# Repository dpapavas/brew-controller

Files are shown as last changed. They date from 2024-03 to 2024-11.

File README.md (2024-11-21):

<!-- -*- coding: utf-8 -*- -->

# Brew controller

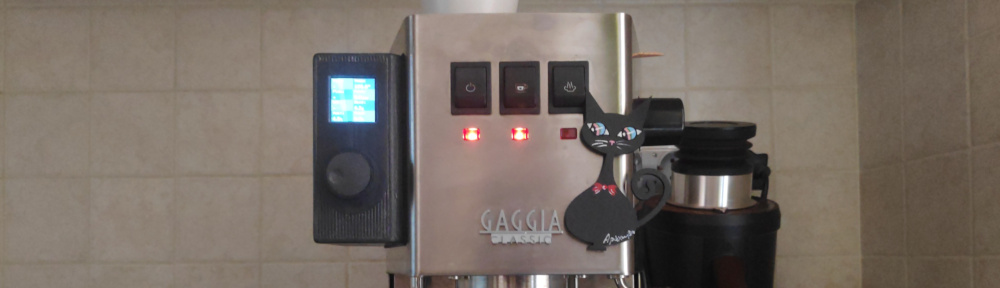
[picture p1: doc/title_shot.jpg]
Title shot


This is a controller module designed as an add-on to the Gaggia Classic espresso
machine, although from a functional perspective it can be used with any "dumb"
espresso machine, i.e. any machine with a simple thermostat for boiler
temperature control and a simple on/off switch for pump control.  It can control
the brew process in both an automatic mode, following a programmed brew profile
based on flow, pressure and/or yield weight, or in manual mode, allowing direct,
real-time control of flow, pressure, or pump power.

## Design

The controller consists of the following parts:

* A pressure sensor, attached to the exit of the boiler, just before the group
  head.

* A flow sensor, attached to the pump inlet.

* A load cell, mounted below the drip tray, weighing the yielded coffee.

* A controller board, consisting of a pair of TRIAC switches, controlling power
  to the boiler and pump and a microcontroller, interfacing the sensors and
  controlling these switches.

* An enclosure and other assorted accessories, used to mount all the above to
  the espresso machine.

The design is freely available, but anyone considering their own build is urged
to read the discussion below, as there are some issues that will need to be
addressed.

## Operation

So, is this useful?  Well, yes, it is. All features, while arguably not
necessary, do offer additional useful control over the brewing process.
Temperature control improves temperature stability and control, allowing the
brewing to be adapted to the coffee at hand and, more importantly, improving the
consistency of the result across multiple shots.  Pump power control, makes
preinfusion possible and, in combination with pressure and flow measurement, it
also makes control of these parameters possible.  Pressure control is useful to
avoid channeling, while flow control can be useful, both to control preinfusion
where pressure has not yet developed and to give some control over brew time.
Weighing the yield allows automatic control of the brew ratio, as well as more
sensible variation of other parameters during the brew process (for instance the
pressure can be tapered off during the final third of the shot in terms of the
yield mass, instead of time).

The following plot is from data recorded by the controller during a programmed
shot.

Shot graph

The machine is already warmed up, as can be seen by the stable temperature (1)
and the small (less than 5% of the total) power needed at the boiler to maintain
it (2).  At about 12s the brew switch is pressed and the shot starts with a
preinfusion phase (3).  The pump is engaged at low power to push water through
the grounds at 3 ml/s.  As this happens, the temperature starts to drop, as cold
water enters the boiler, and power to the boiler is increased in order to
compensate.  Pressure gradually develops as the grounds expand and at 4 bars the
preinfusion phase is terminated (4).  Power to the pump is cut off, flow
vanishes and yield mass starts to rise as coffee starts to drip into the cup.

A blooming phase follows for the next 30s (5), where nothing much happens, apart
from temperature stabilization, a gradual drop-off in pressure and slight
increase in yield, as coffee leaks into the cup.  At 54s, the pump is engaged
once more, at higher power, and pressure is gradually ramped up to 9 bars (6).
Note the high initial flow, as the brew chamber is refilled, followed by a sharp
fall-off as the puck is compressed and pressure develops leading to oscillations
as the PID struggles somewhat to adapt to the complex dynamics.  This
necessitates both a gradual ramp-up in pressure (here from 0 to 9 bars in 5s) as
well as an additional wait time of 5s at 9 bars, while the flow settles.  After
that (7) the brew proceeds at constant flow rate, keeping the flow steady at the
1.7 ml/s it settled at.

In this particular shot, this strategy fails partially.  Maintaining the flow at
the instantaneous value measured at the end of the settling wait interval, leads
to a higher than desired flow and a pressure increase to a bit above 10 bars.
This can be corrected manually, if desired, either by reducing the flow to reduce
the developed pressure, or by reducing the pressure immediately.  No such action
has been taken here and the shot proceeds at a constant 10 bars and about 1.7
ml/s.  Note the disparity in volume and mass, the former of which is calculated
from the flow sensor, while the latter is measured via the load cell.  Some of
the difference is due to the water retained by the grounds, although most of
that has been accounted for, when the volume was reset at the end of the
preinfusion phase (4).  The rest of the difference is owed to inaccuracies in
the flow sensor, which accumulate as its signal is integrated to get the volume.

Finally the brew process is stopped at about 89s, with a total yield of 50g (8)
and pressure and flow drop to zero.  The sudden uptick in mass, is due to the
water remaining in the chamber being evacuated to the drip tray, via the
three-way solenoid valve.

A video recording of the controller brewing this exact shot, can be found
[here](https://youtu.be/QHlgAWKq7i8).

## Build

Although the design works quite well and is, at the time of this writing,
seemingly bug-free and refined enough for efficient and hassle-free daily use,
it does unfortunately suffer from a few design flaws that make it unsuitable for
anyone who might be considering building it.

For one, it was designed by someone that is not an electrical engineer.
Although as much care as possible was taken to ensure a good design, including
simulations and proper calculations where appropriate, the result does have a
few shortcomings which will probably need to be addressed:

* It is based on a Teensy 3.1/3.2 microcontroller, which is sadly no longer in
  production.  Any builds will therefore need to be ported to a more modern
  controller.  This problem is further compounded by the fact that the source
  code is "bare-metal", i.e. no hardware abstraction libraries are used, so that
  porting to a different controller is a non-trivial task.  Note though, that
  teasing out the application specific-code, i.e. the code implementing PID
  control, sensor signal reading and conditioning and rewriting the
  machine-specific parts, such as SPI, I2C, GPIO, timing and interrupt handling
  using a high-level library for the target controller, should not be a
  particularly hard task, given some experience.

* The coffee machine's brew switch, i.e. the one turning on the pump and
  starting the brewing process, is read through a GPIO input that is grounded
  via the switch.  The current design depends on the internal pull-up for this,
  which is too weak and hence prone to EMI.  This should probably be addressed in
  a potential board redesign, by including a stronger external pull-up resistor.

* In the current design, brewing is still controlled by the machine's brew
  switch, which is responsible for turning power to the pump on and off.  While
  this power can then be further controlled via the TRIAC, the three-way
  solenoid valve that is controlled by the same switch cannot.  Relegating this
  task to a relay, controlled by an additional GPIO output could therfore be
  useful, as it would allow automatically stopping the brew process, for
  instance when the desired yield has been achieved.  While this can be done
  now, one still needs to turn the switch off, to turn off the solenoid.  Doing
  this after the pump has been cut off, results in low pressure in the brew
  chamber and hence incomplete evacuation of the remaining brew water,
  nullifying the solenoid valve.

Due to the above, it is not expected that this design will be built by others.
The following discussion will therefore be limited to a general outline of the
build process.  Anyone intending to attempt a build is welcome to open an issue
for further clarifications.

### Parts

The parts needed to populate the board are the following:

|Designator|Description|
|---|---|
|R3,R4|22KΩ, 1W through-hole resistor|
|R5|10KΩ, 1/4W through-hole resistor|
|U5|LD1117, 3.3V, TO-220-3 voltage regulator|
|C4,C2,C5|100nF through-hole ceramic resistor|
|D1|DB104, 400V, 1A bridge rectifier|
|R7,R6|360Ω, 1W through-hole resistor|
|Q1,Q2|2N7000, 0.2A, TO-92 N-Channel MOSFET|
|R8|680Ω, 1W through-hole resistor|
|U3,U2|MOC3021M, 400V optocoupler|
|Q3,Q4|BTA16-800CW 800V, TO-220-3 TRIAC|
|U4|Adafruit MAX31865 Module, or compatible|
|J4|JST XH 2-pin vertical connector|
|R2,R1|82Ω, 1/4W through-hole resistor|
|J2|Pin header, 2.54mm|
|J3|Pin header, 2.54mm|
|J5|Pin header, 2.54mm|
|U1|EL817 or PC817 optocoupler|
|C3|10u radial through-hole capacitor (low profile)|
|U6|Teensy 3.1 or 3.2|
|C1|100n, X2 through-hole capacitor|
|J1|5.08mm terminal block|

The following additional parts are also necessary:

* Heat sinks for the TRIACs.  Extruded aluminum heat sinks of size 46x20x10mm
  fit the enclosure and provide adequate cooling when properly mounted with heat
  sink compound.

* XP POWER ECL10US05-T 5V, 10W AC/DC power supply.

* Waveshare 1.5" RGB OLED Module, based on the SSD1351 controller.

* Waveshare rotation sensor, or similar push-button incremental rotary encoder.

* A PT100 temperature probe, preferably 3-wire.

* XDB-401 pressure sensor, in SS316L steel, 0-12 bar range, G1/8" thread, I2C
  interface.

* Shades Of Coffee Brew pressure gauge adaptor kit, or similar, along with a
  G1/8" female-to-female adaptor, to connect the pressure sensor to the boiler
  output.

* 3.3V hall-effect flow sensor.  The SEN-HZ06D can be used and has a suitably
  low range of 0.05-1.1 L/min.

* Adafruit NAU7802 24-Bit ADC module, or compatible.

* 1Kg 75x12.6x12.6mm load cell.  Mount holes should be M4, 10mm apart to fit the
  base and top plate.

* Shades of coffee slim drip tray.
 
* M3xM5x6mm threaded inserts for the enclosure.

* At least 1mm² silicon wire in various colors for high voltage/current wiring.

* Lower gauge silicon wire for the connection to the the espresso machine's brew
  switch.  Ideally of low enough gauge to allow crimping and fitting a
  Dupont-style terminal.

Finally, some parts need to be 3D printed.  See the [Things](#things) section
below.

# Assembly

Drill a total of six holes on the side of the espresso machine.  The 3D printed
mounting gasket can serve as a stencil to mark the locations and sizes of the
holes.  The four smaller peripheral holes serve to mount the enclosure.  Its
mounting bosses, where the threaded inserts are installed, should be able to
pass through those holes, barely protruding from the other side with the gasket
installed.  The two larger central holes serve to pass wiring into the espresso
machine.  One should be used for high voltage wiring and one for low voltage
wiring, to keep them separated.  Note that it is not absolutely necessary to
fully disassemble the espresso machine in order to drill the holes, although
that is the safest option.  With care, the operation can be carried out with
only the boiler screws and a few of its wires removed and the boiler simply held
out of the way, partially out of the machine.

Install the threaded inserts, assemble the controller board, including the
Teensy and TRIAC heat sinks and mount all boards onto the enclosure.  If the
supplied wiring brackets are used, it is recommended to glue the nuts on their
recesses, as they're otherwise held very loosely and can be a major source of
pain during assembly and repairs.

## Internal wiring

With the boards in place, the following internal wiring connections should be made:

* **Display module**: Attach the supplied 7-pin ribbon to the upper half
    (i.e. the part closest to the Teensy, marked `3V3`, `GND`, ..., `RST`) of
    the `J3` connector, noting the insertion orientation.

* **Rotary encoder**: Attach the supplied 5-pin ribbon to the `J2` connector on
    the board, noting the insertion orientation.

* **Supply**: Attach a suitable JST terminated cable from the output of the PSU
    board to the `J5` connector.  Although the connector is keyed, make sure the
    connector on the side of the controller board hasn't been soldered with
    incorrect orientation.  Also attach a 2-wire cable, terminated on one side
    with a suitable 3-pin JST connector to the input of the PSU board.  The bare
    wires on the other side, should be screwed into the terminal block plugged
    into the `J1` connector, in the pins marked `L` and `N`.  The polarity is
    not important.

After these steps, the assembled enclosure should look like this:

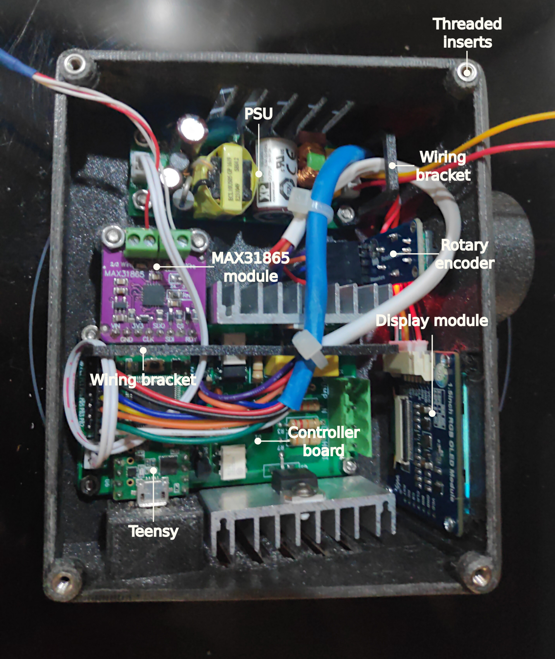
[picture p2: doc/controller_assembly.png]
Controller assembly


## Hardware assembly

Attach all external wiring (see below) to the appropriate controller connectors
and pass the wires through the two chassis holes, keeping high and low voltage
wires separated.  Place the enclosure so that the threaded bosses pass through
the holes drilled in the chassis and fasten it using the supplied countersunk
washers.  The lower washers can be hard to install, but it can be accomplished
using a short magnetic screw driver, if the boiler screws are removed and the
boiler moved out of the way, to gain access through the group head hole in the
chassis.  If the pressure sensor is used, its mount bracket should be used in
place of the washer for the upper hole closest to the middle of the machine.

Once the controller is fastened, the lower boiler thermostat should be removed
and replaced with the PT100 sensor.  The pressure sensor should also be
connected to the pressure gauge kit and mounted in the bracket, secured with a
zip tie passed through the slot in the back of the bracket.  The flow sensor
should be installed in line with the pressure inlet hose.

Two M4x12mm countersunk screws should be installed together with the supplied
"locating pins" in the holes at the top of the load cell base.  These form
locating bosses, mating with the holes at the bottom of the machine's chassis to
keep the base in place.  The load cell can be installed in either side, but the
right hand side is more convenient, as it facilitates the connections between
the controller module and both the load cell and the I2C bus.

The partially assembled scale looks like this:

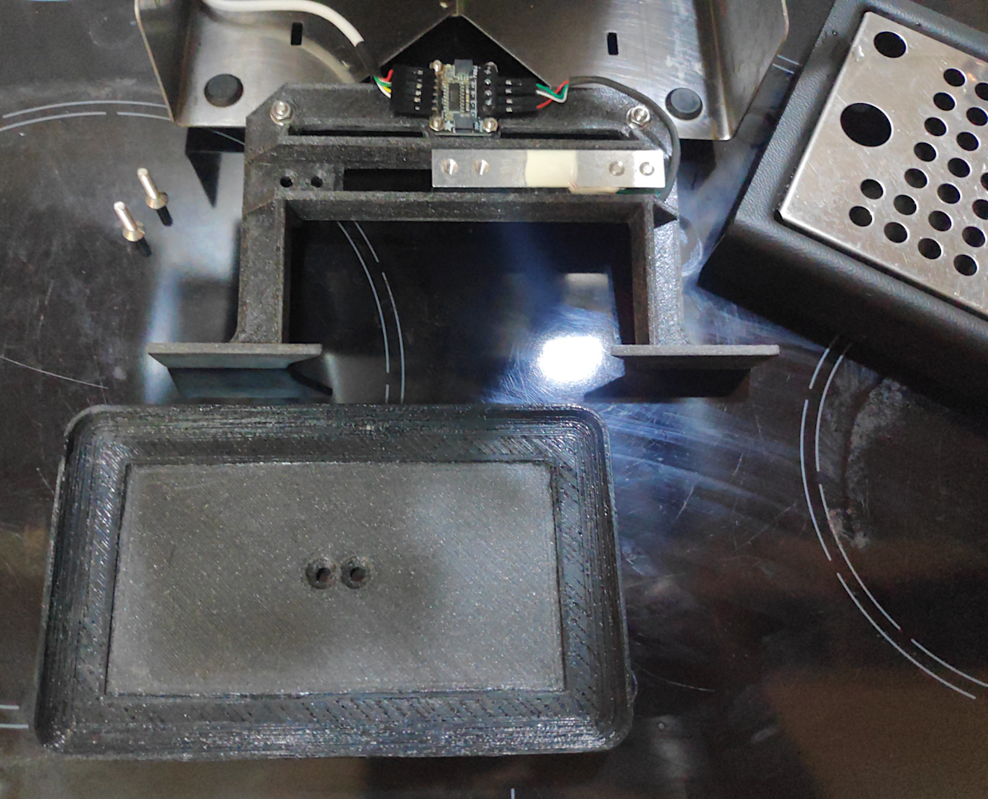
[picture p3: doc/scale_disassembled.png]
Partially assembled scale


The installed scale, can be seen [here](./doc/scale_installed.png).

## External wiring

The instructions below will be brief, intended more as a general strategy for
making the connections to the machine, rather than detailed instructions.  The
photograph should hopefully give a clearify the setup further, but please study
the wiring diagram first and take every care must be taken to ensure the proper
connections are made in a safe manner.

The proposed connections are for the EU model with the ECO timer module.  The
ECO timer will need to be bypassed, so as to gain access to a pair of contacts
at the brew switch for the controller sense connection. A simple wire with two
spade connectors is needed, but kits with installation instructions are also
sold online.

Note that live and neutral are treated loosely here and no care needs to or has
been taken to ensure that they correspond to the live and neutral at the
plug. They will therefore be indicated by "neutral" and "live" below.

### High voltage

* **"Neutral" input**: The "neutral" connection that powers the controller can
    be taken from the brew switch.  This requires a wire with three connectors
    on one end: one male spade connector plugging into the machine's "neutral"
    wire, after removing it from the brew switch, one female spade connector to
    restore the connection to the brew switch and another female spade
    connector, going back to the pump.

    The pump already has a connection for "neutral", but it passes through the
    brew switch, which creates a problem.  As the pump is switched off by the
    switch, back-EMF is created at the pump solenoid, leading to large voltage
    spikes and noise.  This can create all sorts of problems.  For instance it
    can pull the programming pin of the controller low and reboot it into
    programming mode, but it can also create I2C transmission problems, etc.
    Having an unswitched "neutral" connection allows the pump to be switched off
    via the TRIAC, which always ensures switching happens at zero current, hence
    no back-EMF or noise spikes.

    The other, unterminated end should be screwed into the controller's terminal
    block, at the place marked `N`, along with one of the small wires going to
    the PSU input.

* **"Live" input**: The live input can be taken from the lead going to the
    removed thermostat.  The other end should be screwed into to the
    controller's terminal block, at the place marked `L`, along with one of the
    other of the two small wires going to the PSU input.

* **Temperature control**: The other lead removed from the thermostat should be
    connected to the controller's terminal block, at the place marked `HEAT`.
    In this way, the controller's TRIAC switch essenatially assumes the place of
    the OEM thermostat switch.

* **Pump control**: The other terminal of the pump should be screwed into the
    controller's terminal block, at the place marked `PUMP`.  Note that the
    thermal fuse mounted on the pump is now by-passed.  It can be retained
    either by cutting and reusing the existing part, or by using a spare part,
    connected in-line with the wire going to the controller.

* **Solenoid snubber**: The three-way solenoid valve can generate noise, both
    due to the inrush current at turn-on, as well as due to the back-EMF induced
    voltage spike at turn-off.  The latter is more pronounced and can generate
    all sorts of havoc, such as resetting the controller, pulling encoder lines
    low generating phantom button presses, etc.  A simple (0.1 μF, 100 Ω, 1/2W,
    600 VAC) RC snubber should therefore be installed accross its line and
    neutral terminals to alleviate such problems.  Snubbers such as this can be
    readily found as a single discrete part, which, together with a few
    terminals and short wiring, can be attached to the valve without
    modifications to the OEM wiring.

### Low voltage

* **I2C bus**: A 4 core shielded cable should be used for the I2C bus.  At one
    end the following connections need to be made at the controller, at connetor
    `J3`:
        - `GND` to I2C ground
        - `PC2` to I2C +3.3V
        - `PB2` to I2C SCL
        - `PB3` to I2C SDA

    At the other end the cable should be connected to the pressure sensor and
    the load cell sensor board.  A thin enough cable can be routed through a gap
    in the mahine's chassis and behind and below the water tank.  The I2C wiring
    should be kept as short as possible, leaving enough slack to pull out the
    load cell frame when required.  The shield wire should be attached to the
    ground at both ends.

* **Flow sensor**: The wires from the flow sensor should be connected to the
    controller board, at connetor `J3`, as follows:
        - `PD5` to sensor +3.3V
        - `PD6` to sensor ground
        - `PC1` to sensour output

* **Temperature sensor**: The PT100 wires should be connected to the MAX31865
    module.  Consult its datasheet for the proper connections, as well as solder
    jumper configuration.

* **Brew switch sense**: The brew switch contacts left unused by the ECO timer
    by-pass should be connected to the controller, at the connetor `J5`.  One of
    the connectors pins is a ground pin and this should also be connected to the
    machine's chassis ground.  This connection serves to reference the
    controller's ground to the mains ground, preventing ground loops when the
    USB connector is attached to a mains-powered desktop computer.  It can be
    conveniently established with a female spade terminal, at the unused male
    spade forming part of the thermal fuse bracket screwed to the top of the
    boiler.

    A 100nF capacitor should also be soldererd between these two wires.  This
    serves to prevent votlage dips induced due to the large voltage (and hence
    current) differentials as the TRIAC switches the boiler on mid-cycle.

With all connections made, the machine's wiring should look similar to this:

Sensors and wiring

# Software

To compile the firmware, you'll need the `gcc-arm-none-eabi` toolchain and the
Teensly CLI loader. With everything installed, compiling and loading the
firmware can be accomplished with:

```bash
$ cd src/
$ make all
$ make install
```

The firmware boots up in "automatic" mode; pressing the brew switch at this
point will execute the loaded program.  Pressing the encoder wheel button cycles
through the various manual modes, allowing manual control of the flow, pressure,
heat and pump power.  These are useful, both to execute on-the-fly, manually
controlled shot profiles, as well as to carry out various maintenance operations
(rinsing the group headed, backflushing, etc.).  Note that no manual control
over the scale is necessary, as it tares automatically, whenever a large enough
change in mass is detected (e.g. a cup or bean dosing tray is placed on it).

## USB console

With the controller connected to a computer via USB, a rudimentary serial
console is available, affording some manual control of the executing firmware,
as well as querying and logging its state.  How it can be accessed, depends on
your platform.  For instance, on GNU/Linux, it can be accomplished with the
`socat` program with:

```bash
$ socat - /dev/ttyACM0,raw,echo=0
```

The following commands are available:

* `r`: Reset the controller.
* `b`: Reboot the controller into programming mode.

* `l[t|p|m|f][N]`: Toggle logging of temperature (`t`),
    pressure (`p`), mass (`m`), or flow (`f`), or print `N` log lines if an
    optional trailing number is provided.  The output consists of lines of
    comma-separated values, corresponding to time, value, derivative, raw value,
    and raw code, respectively.  The value is the filtered instantaneous value
    of the logged parameter, with the unfiltered value also available, to aid in
    tuning the filtering if desired.  The raw code is the data read from the
    sensor; mostly useful in debugging sensor communication.  Free-running
    logging can be stopped by issuing any logging command, including a simple
    `l`.

    For example `lt10` would display 10 lines of temperature data, `lp` would
    turn on pump logging and `l` would turn it off again.

* `l(T|P|F)[N]`: Toggle logging of temperature (`T`), pressure
    (`P`), or flow (`F`) PID control.  Similar to the above, only the
    lines contain time, PID output (i.e. heat/pump power), PID input
    (i.e. temperature, pressure, etc.), PID set point and PID proportional,
    integral and derivative terms.  Useful in tuning the PID parameters.

* `ls[N]`: Toggle "shot" logging.  Similar to the above, but the lines contain
    time, temperature, pressure, flow, volume, mass and heat and pump power.
    Useful in producing shot graphs, such as the one in this document.

* `lc`: Toggles "click" logging, useful in debugging the operation of the
    rotary encoder wheel.

* `s[h|p][d|p|f][N]`: Without a setting `N`, prints the current heat (`h`) or
    pump (`p`), delay (`d`), power (`p`) or flow (`f`) setting.  All are
    expressed in percentages, from 0 to 100.  Delay is simply the dalay before
    the TRIAC turns on the device in question, i.e. the complement of duty.
    Power is a setting in terms of percent of full power, from which a delay
    setting is calculated.  Flow, is only accepted for the pump and is the same
    as power, with a slight normalization as anything below 20% power doesn't
    really produce any flow to speak ok.

    For example, `shp` would print the current heat power setting and `spd50`
    would turn on power to the pump for half the mains voltage cycle.

* `c[h|p|f][SET,Kp,Ti,Td]`: With no settings, prints current heat (`h`) pump
    (`p`), or flow (`f`) PID configuration as a series of comma-separated
    numbers, including set point, gain, integration time, derivative time and
    current error integral of the PID.  The first three of the above parameters
    can be changed, by specifying new values.  The integral is always reset when
    any PID configuration value is changed.

    For example, `ch94` will only change the temperature setpoint to 94 keeping
    other heat PID parameters unchanged, while `cp3,0.35` will set the pump PID
    to 3 bars with gain equal to 0.35.

* `ci[SLAVE,ADDR,VAL]`: Query or configure I2C devices.  With only the slave
    specified, probe this slave.  This will result in an error if the slave is
    not on-line.  If a register address is also specified, read this address and
    return its contents in decimal, hexadecimal and binary forms.  If a value is
    also specified, write this value to the specified address. All parameters
    are in hexadecimal notation.

    For example, `ci54,0` reads register 0 of the NAU78802, while `cida,1,20`
    writes 0x20 to register 1 of the NSA2862X inside the pressure sensor.

* `z[f|m]`: Resets the calculated volume (`f`) to zero, or tares mass
    (`m`).

* `p[l|,STAGE,...]`: Without any arguments, a plain `p` prints the current
    programmed brew profile.  When `l` is specified the last captured profile
    log is printed, otherwise programs the new brew profile.

    The program, consists of a set of stages, separated by commas.  Each stage
    is a separate phase of the brew process, where some output variable, which
    can be either flow (`f`), pressure (`p`) or pump power (`w`) is controlled
    based on some measured input variable, either shot time (`t`), current
    pressure (`p`), current flow (`f`), current volume (`v`), or current mass
    (`m`).  Conceptually, it can be though of as a graph, with the input
    (measured) variable on the x axis and the output (controlled) variable on
    the y axis.  Both axes can be specified in one of three modes: absolute
    (`a`) where the value is given in absolute terms, relative (`r`) where the
    value is given relative to what it was at the beginning of the phase and
    ratiometric (`q`) where it is specified as a multiple of what it was at the
    beginning of the phase.

    Each phase is specified as `input;output;point1;point2;...;commands`, where
    `input` and `output` each consist of two letters, specifying the input and
    output mode and variable, points are specified as `(x,y)` and commands can be
    one or more letters indicating that the shot time (`t`), volume (`v`), and
    mass (`m`) should be reset at the end of the phase, or `b`, which moves back
    one section, allowing unconditional looping.  Both the input and output
    values of the first point on each phase may be absent, indicating that the
    current value should be used.

    Consider the following program for example:

    ```
    ap;af;(0,3);(4,3);v,rt;ap;(0,);(1,0);(30,0);(35,9);(40,9);,av;qf;(0,);(+inf,1);
    ```

    It has three phases: the first preinfusion phase (`ap;af;(0,3);(4,3);v`)
    controls flow based on pressure and specifies a constant flow of 3 ml/s
    until the pressure reaches 4 bars.  The volume is then reset as we don't
    care about the water in the puck, only the yield.  The next phase
    (`rt;ap;(0,);(1,0);(30,0);(35,9);(40,9);`), controls pressure base on
    relative time, dropping the pressure to 0 within 1 second and keeping it
    there for 29 more seconds, until half a minute has passed from the beginning
    of the second phase.  The pressure is then ramped up to 9 bars in 5s and
    kept there for 5s more.  Finally the third phase (`rt;qf;(0,);(+inf,1);`)
    controls ratiometric flow based on relative time, and essentially keeps
    whatever flow resulted from the ramp-up to 9 bars at the end of the previous
    phase constant (a ratio of 1) forever, which is to say, until the brew
    switch is turned to the off position.

# Things

|STL|Description|
|---|---|
|[things/enclosure.stl](./things/enclosure.stl)|The enclosure for the controller board and peripherals.  It is mounted onto the side of the espresso machine.|
|[things/controller_bracket.stl](./things/controller_bracket.stl)|A bracket that can be mounted on the controller board, to serve as a tying post for the wiring.|
|[things/psu_bracket.stl](./things/psu_bracket.stl)|Same as above, for the PSU board.|
|[things/mount_gasket.stl](./things/mount_gasket.stl)|A gasket, to be printed in TPU and placed between the enclosure and the espresso machine's chassis.|
|[things/mount_washer.stl](./things/mount_washer.stl)|At least three of these are necessary; four if not using the pressure sensor mount.  They're used as washers for the M3 countersunk screws fastening the enclosure onto the machine's side.|
|[things/knob.stl](./things/knob.stl)|A knob for the rotary enocoder.  This is optional; any compatible knob can be used.|
|[things/knob_sleeve.stl](./things/knob_sleeve.stl)|A rubber sleeve for the knob, to be printed in TPU.|
|[things/nut.stl](./things/nut.stl)|An M7 flanged nut for the rotary encoder.  Not needed if one was supplied with the encoder.|
|[things/usb_plug.stl](./things/usb_plug.stl)|A plug for the USB port opening, to be printed in TPU.|
|[things/sensor_mount.stl](./things/sensor_mount.stl)|A mount bracket for the pressure sensor.|
|[things/load_base.stl](./things/load_base.stl)|The base of the weighing assembly, mounted in the place of the OEM drip tray.|
|[things/load_pin.stl](./things/load_pin.stl)|Locating pins, fastened with M4 countersunk screws on the bottom of the base, mating with the holes on the bottom of the espresso machine.|
|[things/load_plate.stl](./things/load_plate.stl)|The top plate, mounted on the load cell.|
|[things/load_plate_frame.stl](./things/load_plate_frame.stl)|A rubber frame for the top plate, to be printed in TPU and glued onto it.|

These designs were created using [Gamma](https://github.com/dpapavas/gamma) and
can therefore be modified to suit different parts or layouts.  Their source
files are located in
[/scheme](https://github.com/dpapavas/brew-controller/tree/master/scheme).

# Simulations

The simulations in [spice/](./spice) can be run with
[ngspice](https://ngspice.sourceforge.io/) and
[lepton-eda](https://github.com/lepton-eda/lepton-eda).  They include
simulations for the TRIAC drivers and RC snubber and can be useful when trying
out modifications to these circuits.

The following files are also needed to run the simulations, but haven't been
added to the distribution, since they are proprietary.  They can be readily
downloaded from the part manufacturers websites:

- `spice/1n4007.rev0.lib`
- `spice/2n7000.rev0.lib`
- `spice/MOC302X.lib`
- `spice/st_standard_snubberless_triacs.lib`

## License

The Scheme code in [scheme/](./scheme), is distributed under the [GNU
Affero General Public License Version 3](./LICENSE.AGPL).

The firmware sources in [src/](./src), as well as the controller PCB
design residing in [kicad/](./kicad/), is distributed under the [GNU
General Public License Version 3](./LICENSE.GPL).

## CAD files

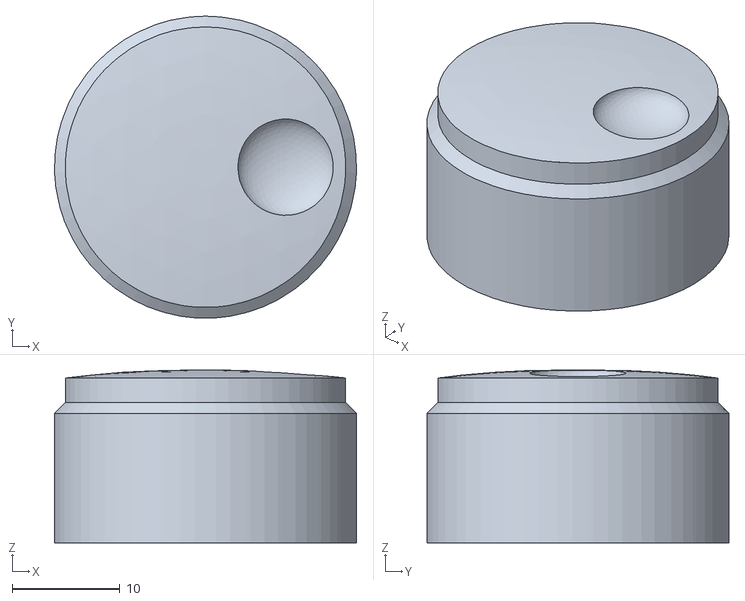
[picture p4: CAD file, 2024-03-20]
things/knob.stl
28.0 x 28.0 x 16.0

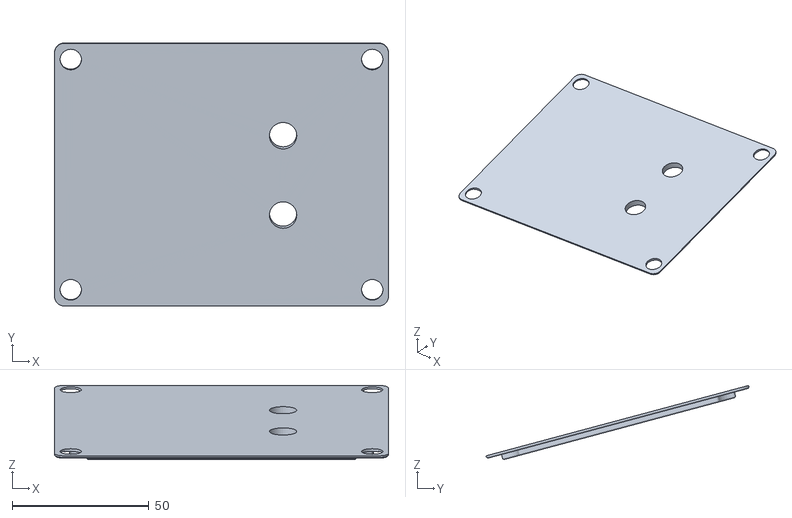
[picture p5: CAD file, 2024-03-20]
things/mount_gasket.stl
122.0 x 96.1 x 27.1

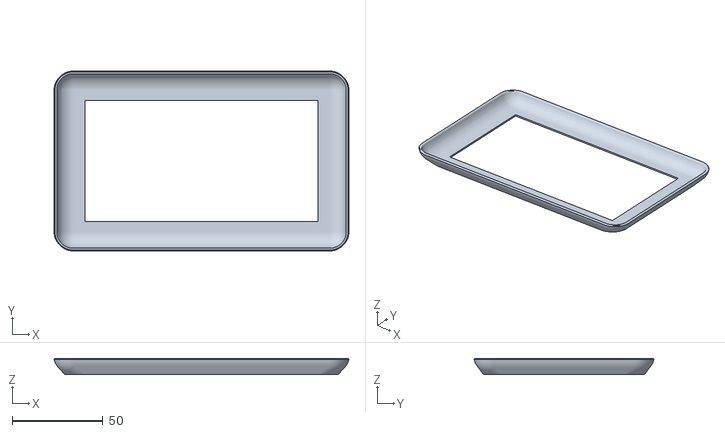
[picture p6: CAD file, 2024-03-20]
things/load_plate_frame.stl
162.9 x 99.4 x 9.00

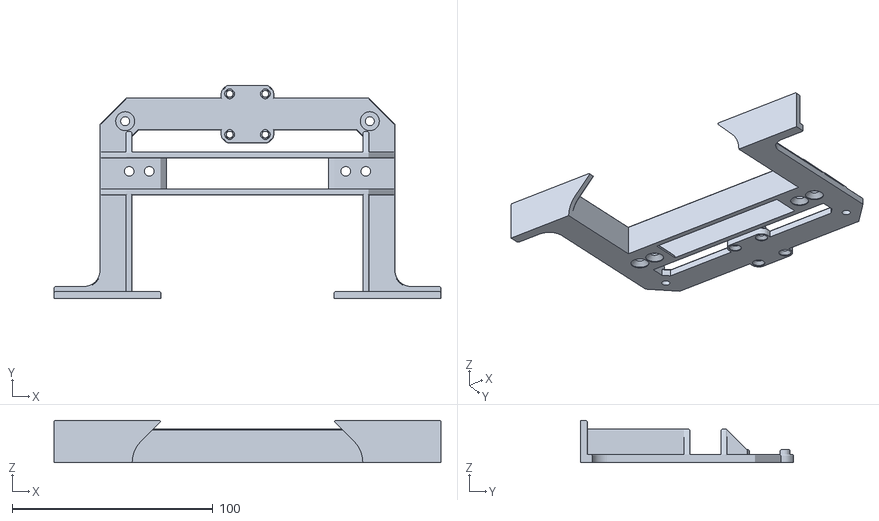
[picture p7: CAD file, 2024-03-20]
things/load_base.stl
193.0 x 106.4 x 21.0

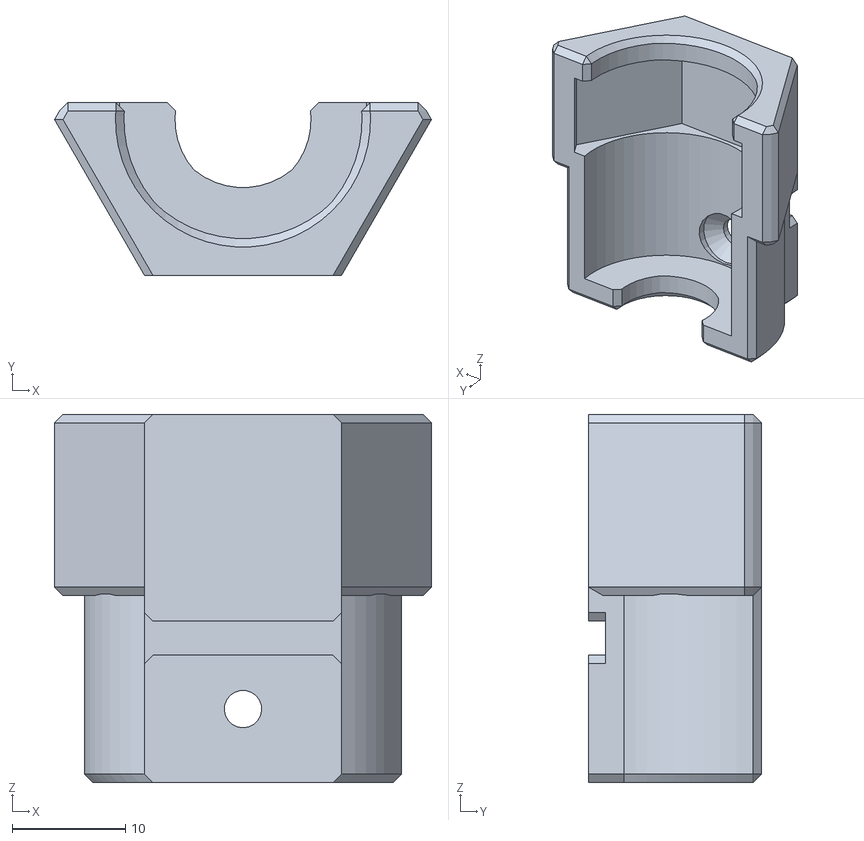
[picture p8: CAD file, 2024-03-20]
things/sensor_mount.stl
33.3 x 15.3 x 32.5

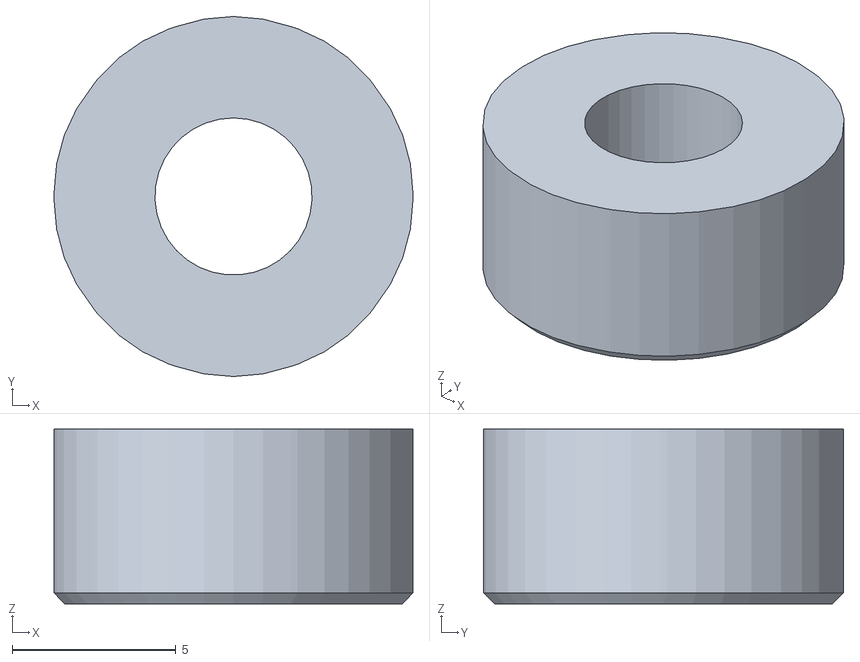
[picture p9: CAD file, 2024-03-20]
things/load_pin.stl
11.0 x 11.0 x 5.33

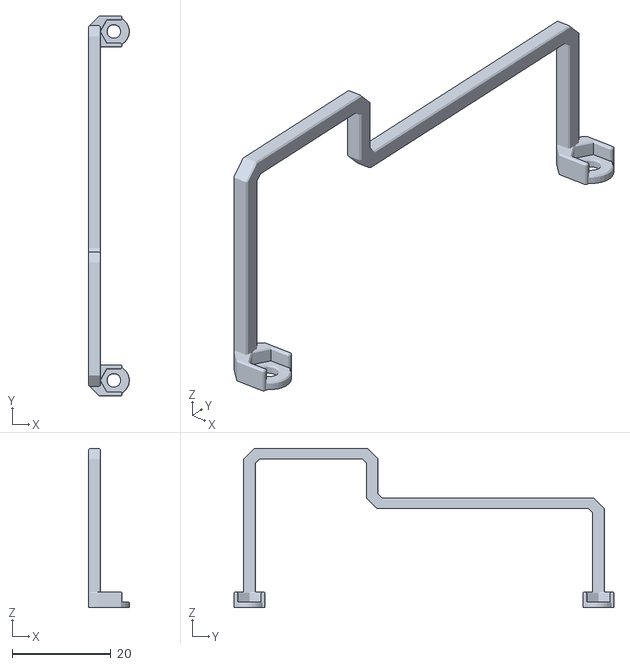
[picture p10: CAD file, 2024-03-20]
things/controller_bracket.stl
8.26 x 76.9 x 32.2

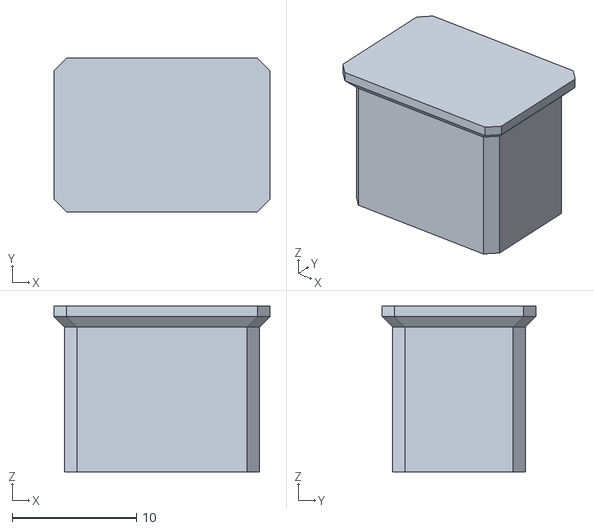
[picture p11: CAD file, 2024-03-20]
things/usb_plug.stl
17.4 x 12.4 x 13.3

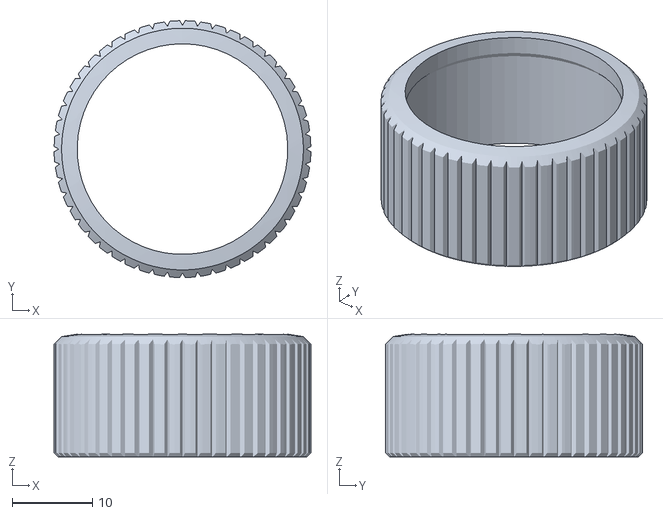
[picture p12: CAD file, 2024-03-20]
things/knob_sleeve.stl
32.0 x 31.9 x 15.3

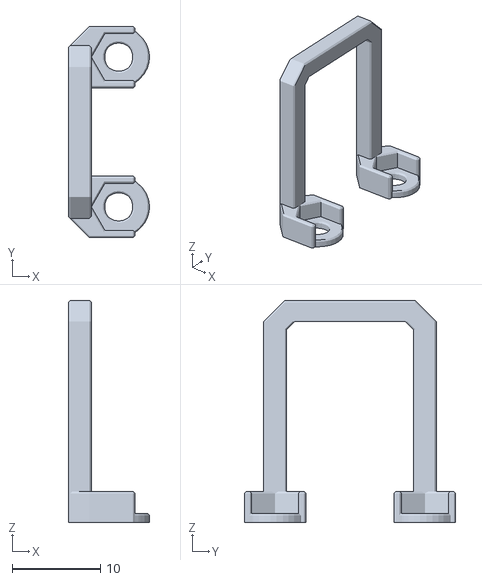
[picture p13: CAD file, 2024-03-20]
things/psu_bracket.stl
9.20 x 24.0 x 25.2

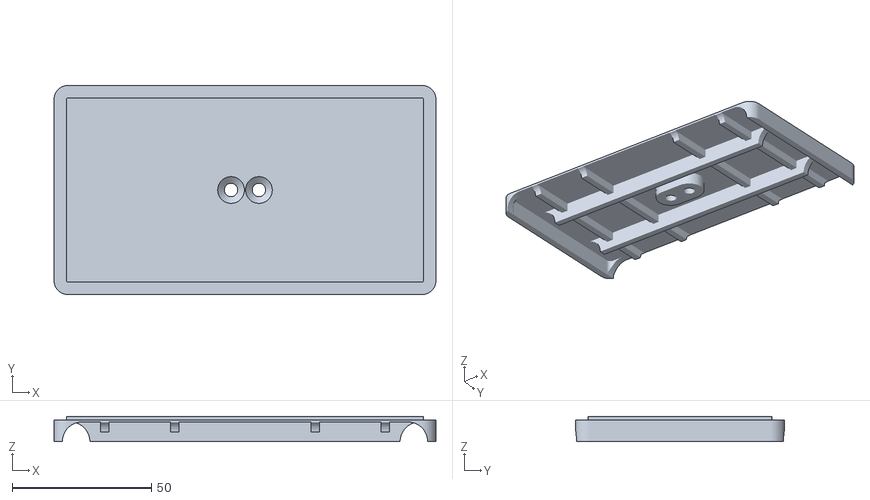
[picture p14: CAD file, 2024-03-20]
things/load_plate.stl
137.0 x 75.0 x 9.00

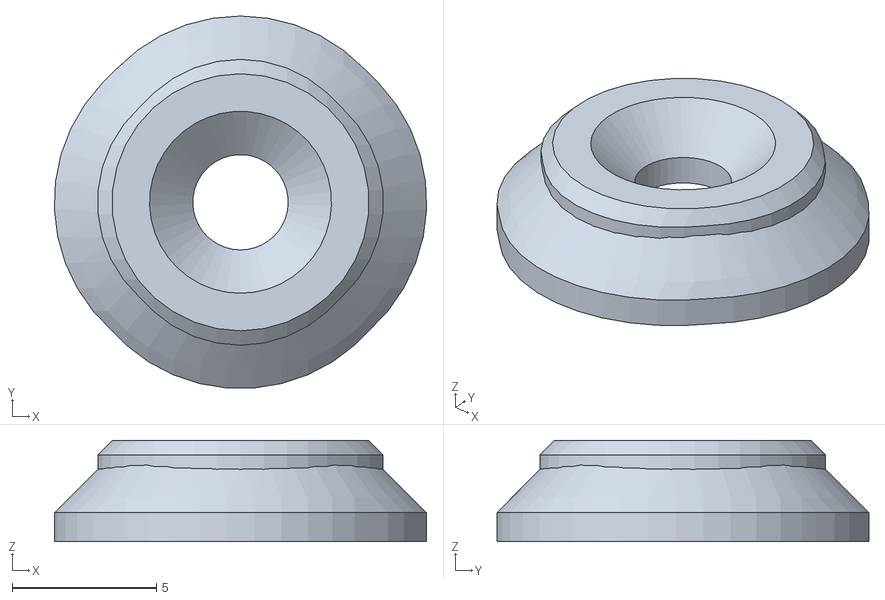
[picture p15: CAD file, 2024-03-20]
things/mount_washer.stl
12.9 x 12.9 x 3.50

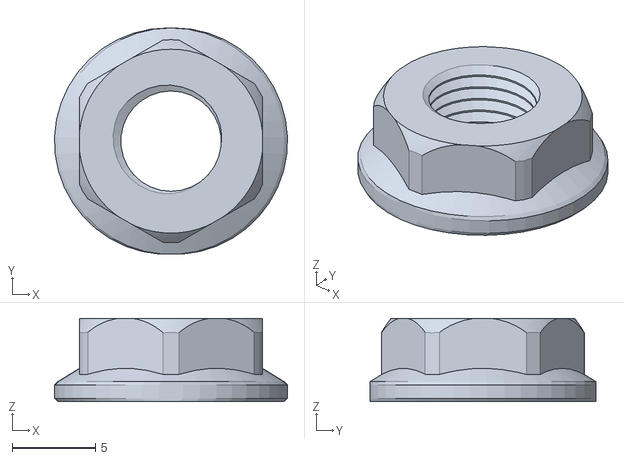
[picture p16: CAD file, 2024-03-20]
things/nut.stl
14.0 x 13.6 x 5.00

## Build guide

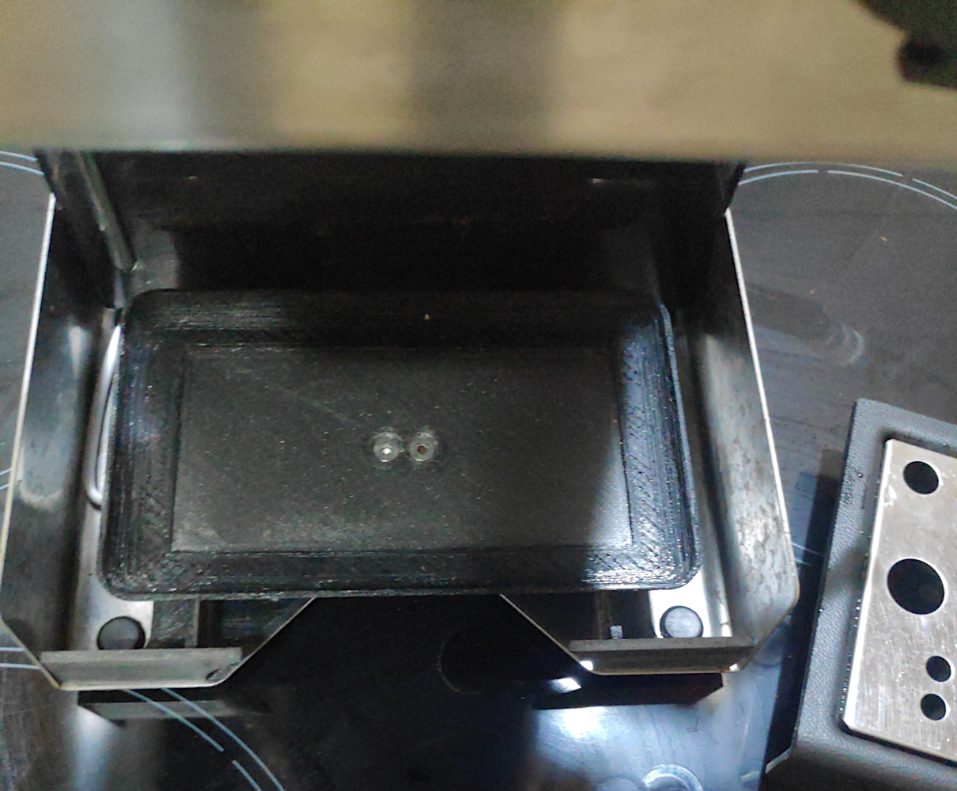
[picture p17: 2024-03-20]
doc/scale_installed.png

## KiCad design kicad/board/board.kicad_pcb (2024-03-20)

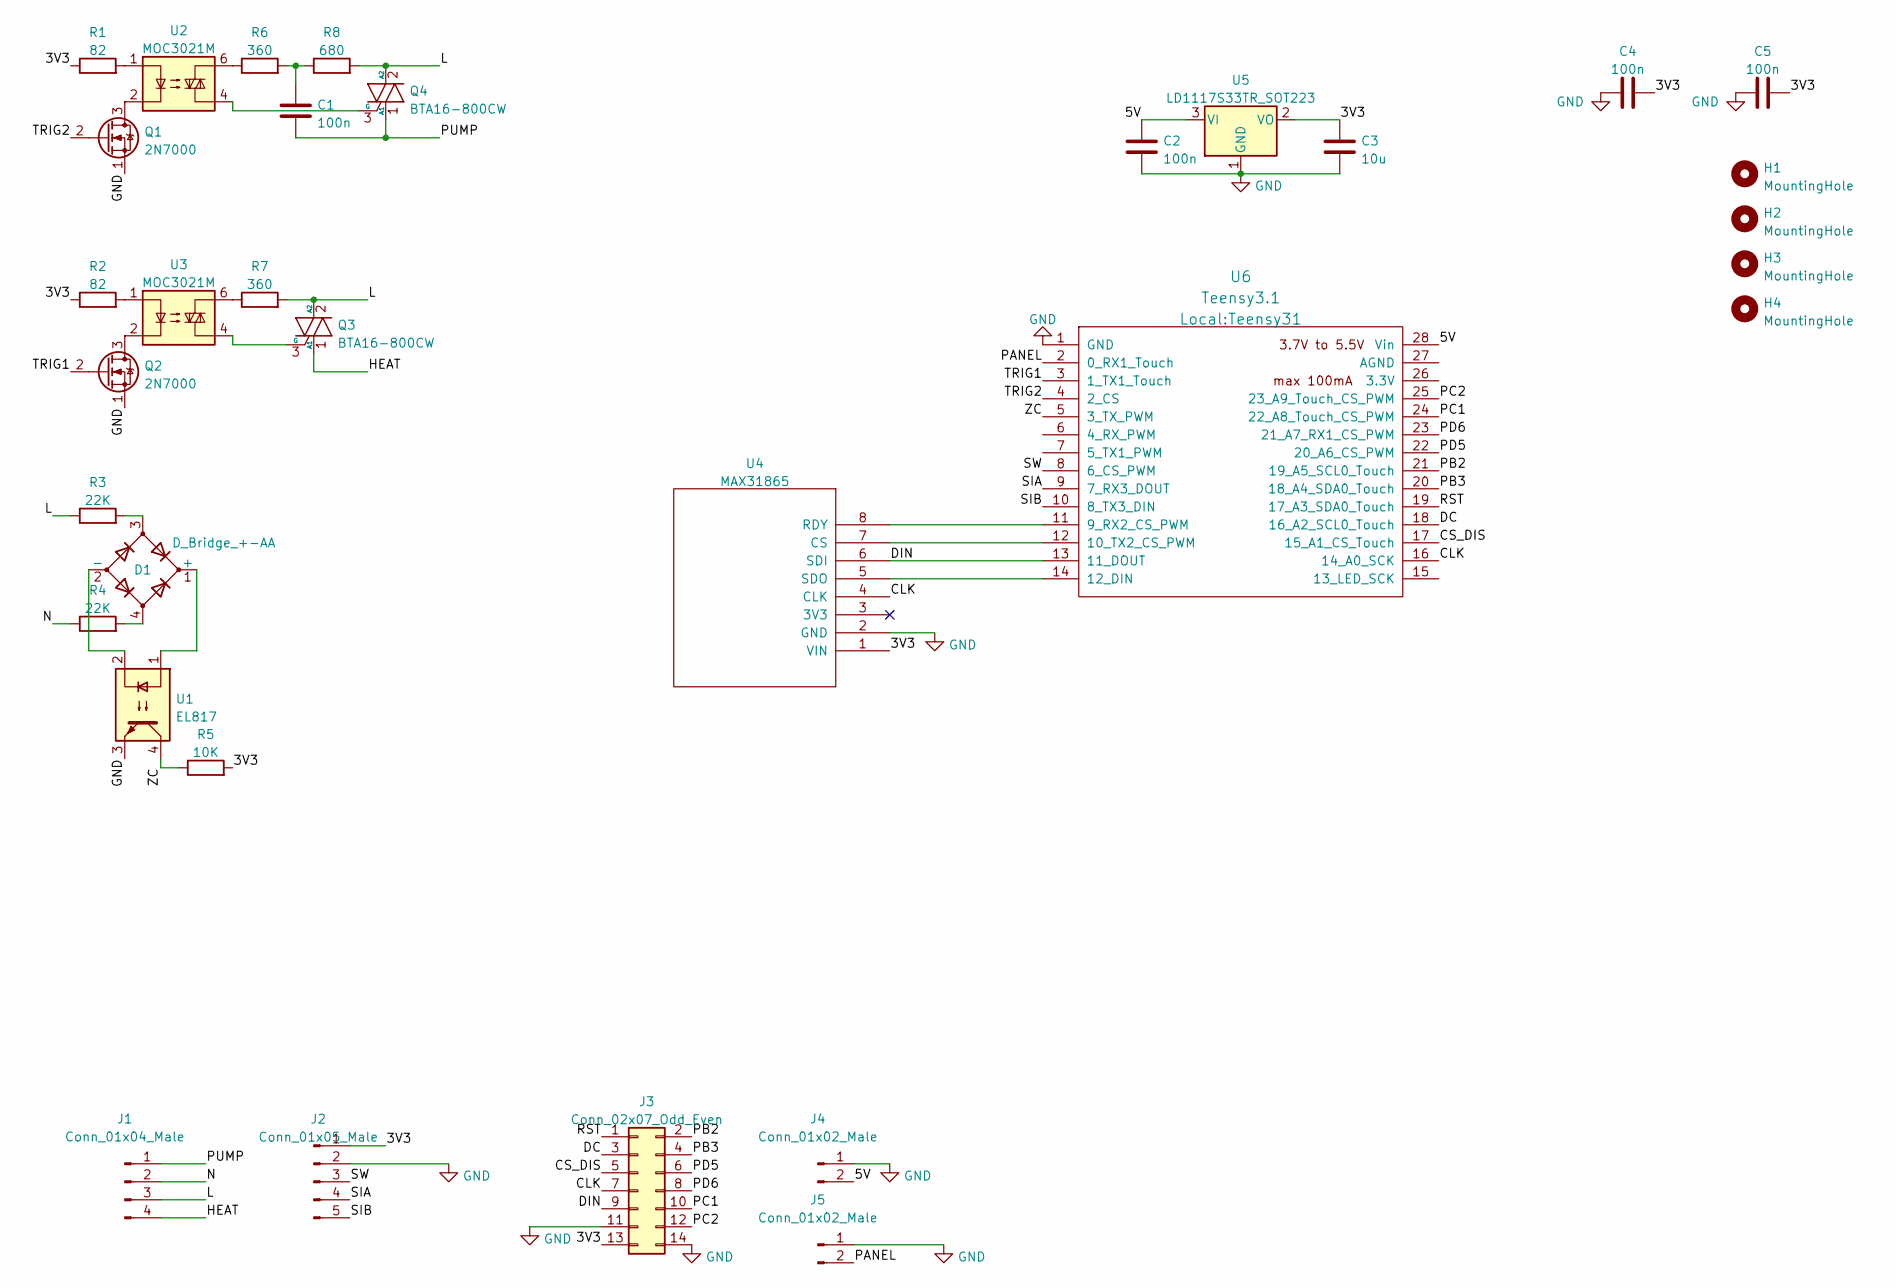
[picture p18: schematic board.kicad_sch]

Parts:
C1: 100n; C_Rect_L18.0mm_W6.0mm_P15.00mm_FKS3_FKP3
C2, C4, C5: 100n; C_Disc_D5.0mm_W2.5mm_P2.50mm
C3: 10u; CP_Radial_D5.0mm_P2.50mm
D1: D_Bridge_+-AA; Diode_Bridge_DIP-4_W7.62mm_P5.08mm
H1, H2, H3, H4: MountingHole; MountingHole_2.7mm_M2.5_ISO7380
J1: Conn_01x04_Male; TerminalBlock-4_P5.08mm
J2: Conn_01x05_Male; PinHeader_1x05_P2.54mm_Vertical
J3: Conn_02x07_Odd_Even; PinHeader_2x07_P2.54mm_Vertical
J4: Conn_01x02_Male; JST_XH_B2B-XH-AM_1x02_P2.50mm_Vertical
J5: Conn_01x02_Male; PinHeader_1x02_P2.54mm_Vertical
Q1, Q2: 2N7000; TO-92_Inline_Wide
Q3, Q4: BTA16-800CW; TO-220-3_Vertical_Heatsink
R1, R2: 82; R_Axial_DIN0207_L6.3mm_D2.5mm_P7.62mm_Horizontal
R3, R4: 22K; R_Axial_DIN0309_L9.0mm_D3.2mm_P12.70mm_Horizontal
R5: 10K; R_Axial_DIN0207_L6.3mm_D2.5mm_P7.62mm_Horizontal
R6, R7: 360; R_Axial_DIN0309_L9.0mm_D3.2mm_P12.70mm_Horizontal
R8: 680; R_Axial_DIN0309_L9.0mm_D3.2mm_P12.70mm_Horizontal
U1: EL817; DIP-4_W7.62mm
U2, U3: MOC3021M; DIP-6_W7.62mm
U4: MAX31865; MAX31865 Module
U5: LD1117S33TR_SOT223; TO-220-3_Horizontal_TabDown
U6: Teensy3.1; Teensy31

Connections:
/3V3: C3.1, C4.2, C5.2, J2.1, J3.13, R1.1, R2.1, R5.2, U4.1 (VIN), U5.2 (VO)
/5V: C2.1, J4.2, U5.3 (VI), U6.28 (Vin)
/CLK: J3.7, U4.4 (CLK), U6.16 (14_A0_SCK)
/CS_DIS: J3.5, U6.17 (15_A1_CS_Touch)
/DC: J3.3, U6.18 (16_A2_SCL0_Touch)
/DIN: J3.9, U4.6 (SDI), U6.13 (11_DOUT)
/HEAT: J1.4, Q3.1 (A1)
/L: J1.3, Q3.2 (A2), Q4.2 (A2), R3.1, R7.2, R8.2
/N: J1.2, R4.1
/PANEL: J5.2, U6.2 (0_RX1_Touch)
/PB2: J3.2, U6.21 (19_A5_SCL0_Touch)
/PB3: J3.4, U6.20 (18_A4_SDA0_Touch)
/PC1: J3.10, U6.24 (22_A8_Touch_CS_PWM)
/PC2: J3.12, U6.25 (23_A9_Touch_CS_PWM)
/PD5: J3.6, U6.22 (20_A6_CS_PWM)
/PD6: J3.8, U6.23 (21_A7_RX1_CS_PWM)
/PUMP: C1.2, J1.1, Q4.1 (A1)
/RST: J3.1, U6.19 (17_A3_SDA0_Touch)
/SIA: J2.4, U6.9 (7_RX3_DOUT)
/SIB: J2.5, U6.10 (8_TX3_DIN)
/SW: J2.3, U6.8 (6_CS_PWM)
/TRIG1: Q2.2 (G), U6.3 (1_TX1_Touch)
/TRIG2: Q1.2 (G), U6.4 (2_CS)
/ZC: R5.1, U1.4, U6.5 (3_TX_PWM)
GND: C2.2, C3.2, C4.1, C5.1, J2.2, J3.11, J3.14, J4.1, J5.1, Q1.1 (S), Q2.1 (S), U1.3, U4.2 (GND), U5.1 (GND), U6.1 (GND)
unnamed: C1.1, R6.2, R8.1
unnamed: D1.1 (+), U1.1
unnamed: D1.2 (-), U1.2
unnamed: D1.3, R3.2
unnamed: D1.4, R4.2
unnamed: Q1.3 (D), U2.2
unnamed: Q2.3 (D), U3.2
unnamed: Q3.3 (G), U3.4
unnamed: Q4.3 (G), U2.4
unnamed: R1.2, U2.1
unnamed: R2.2, U3.1
unnamed: R6.1, U2.6
unnamed: R7.1, U3.6
unnamed: U4.5 (SDO), U6.14 (12_DIN)
unnamed: U4.7 (CS), U6.12 (10_TX2_CS_PWM)
unnamed: U4.8 (RDY), U6.11 (9_RX2_CS_PWM)

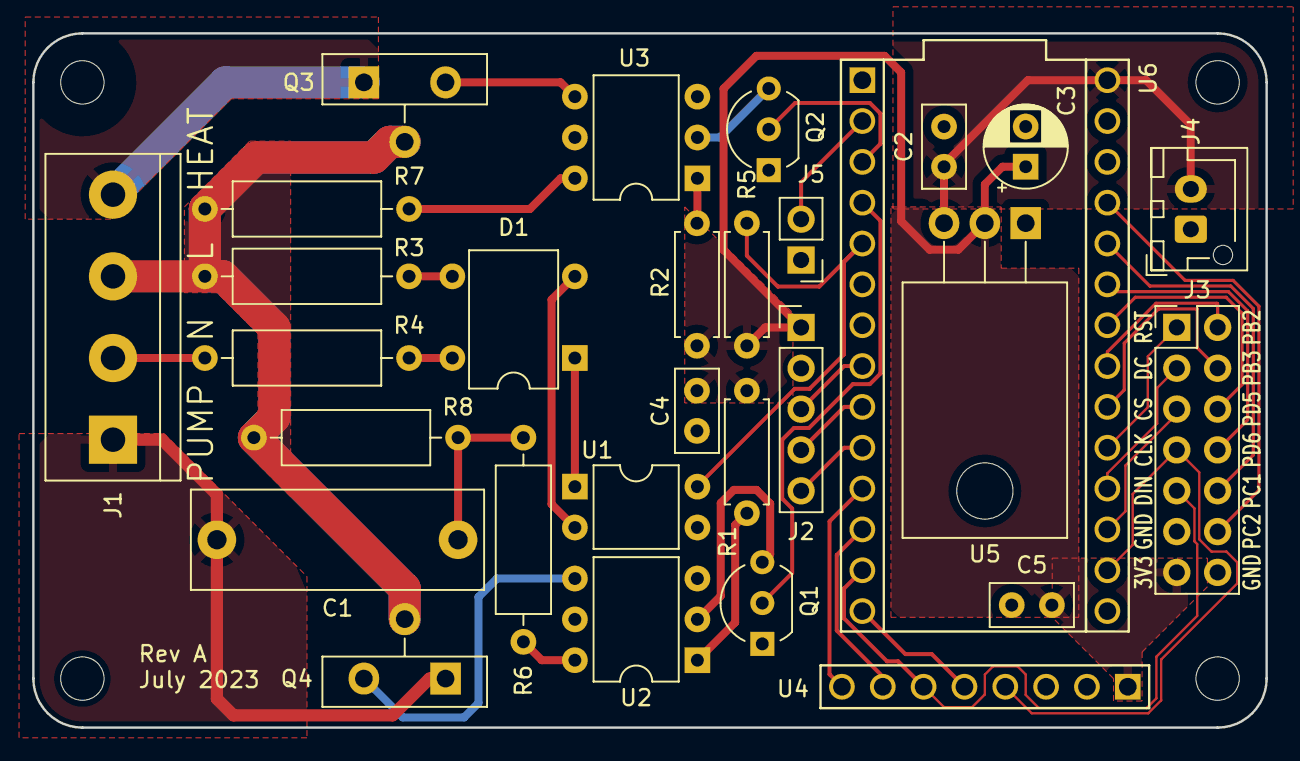
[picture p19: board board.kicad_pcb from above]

Board: 2 copper layers, 76.7 x 43.2 mm, 33 parts (0 on the bottom side), 41 nets.

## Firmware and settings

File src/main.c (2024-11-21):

/* Copyright (C) 2024 Papavasileiou Dimitris
 *
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
 * You should have received a copy of the GNU General Public License
 * along with this program.  If not, see <http://www.gnu.org/licenses/>.
 */

#include <ctype.h>
#include <stdlib.h>
#include <string.h>
#include <math.h>

#include "callbacks.h"
#include "fonts.h"
#include "i2c.h"
#include "mk20dx.h"
#include "peripherals.h"
#include "profile.h"
#include "time.h"
#include "uassert.h"
#include "usb.h"

static bool update_display = true;

#define K_U 0.125
#define P_U 16.5

struct pid temperature_pid = {0.6 * K_U, 0.5 * P_U, 0.125 * P_U, NAN};

#undef K_U
#undef P_U

#define K_U 0.2
#define P_U 1.5

struct pid pressure_pid = {0.6 * K_U, 0.5 * P_U, 0.125 * P_U, NAN};

#undef K_U
#undef P_U

#define K_U 0.24
#define P_U 0.6

struct pid flow_pid = {K_U / 3, 0.5 * P_U, P_U / 3, NAN};

#undef K_U
#undef P_U

double strtod(const char *s, char **e)
{
    int n = 0, i = 1, u = 0;
    bool p = false;

    if (!strncmp(s, "nan", 3)) {
        if (e) {
            *e = (char *)s + 3;
        }

        return NAN;
    }

    if (*s == '-') {
        i = -1;
        s++;
    } else if (*s == '+') {
        s++;
    }

    if (!strncmp(s, "inf", 3)) {
        if (e) {
            *e = (char *)s + 3;
        }

        return i * INFINITY;
    }

    while (*s) {
        if (isdigit((int)*s)) {
            u = u * 10 + *s++ - '0';

            if (p) {
                n--;
            }
        } else if (!p && *s == '.') {
            p = true;
            s++;
        } else {
            break;
        }
    }

    if (e) {
        *e = (char *)s;
    }

    return (i * u * exp10(n));
}

static int log_line_count;

#define LOGGING_CALLBACK_BODY(FMT, ...)         \
    {                                           \
        if (log_line_count == 0) {              \
            return true;                        \
        }                                       \
                                                \
        if (log_line_count > 0) {               \
            log_line_count--;                   \
        }                                       \
                                                \
        uprintf(FMT, __VA_ARGS__);              \
                                                \
        return false;                           \
    }

static bool turn_logging_callback(int delta)
LOGGING_CALLBACK_BODY("wheel %d\n", delta)

static bool click_logging_callback(bool down)
LOGGING_CALLBACK_BODY("wheel %s\n", down ? "down" : "up")

static bool panel_logging_callback(bool down)
LOGGING_CALLBACK_BODY("panel %s\n", down ? "down" : "up")

static bool shot_logging_callback(void)
LOGGING_CALLBACK_BODY(
    "%.3f, %.3f, %.3f, %.3f, %.3f, %.3f, %.3f, %.3f\n",
    (double)get_time(),
    (double)temperature_filter.y,
    (double)pressure_filter.y,
    (double)get_flow(),
    (double)get_volume(),
    (double)mass_filter.y,
    (double)get_heat_power(),
    (double)get_pump_flow());

#define DEFINE_SENSOR_LOGGING_CALLBACK(WHAT)                            \
static bool WHAT ##_logging_callback(                                   \
    double y, double dy, double t, double dt,  double y_raw, int32_t c) \
LOGGING_CALLBACK_BODY(                                                  \
    "%.3f, %.3f, %.3f, %.3f, %d\n",                                     \
    (double)t, (double)y, (double)(dy / dt), (double)y_raw, c)

DEFINE_SENSOR_LOGGING_CALLBACK(temperature)
DEFINE_SENSOR_LOGGING_CALLBACK(pressure)
DEFINE_SENSOR_LOGGING_CALLBACK(mass)
DEFINE_SENSOR_LOGGING_CALLBACK(flow)

#define DEFINE_PID_LOGGING_CALLBACK(WHAT, X)                            \
static bool WHAT ##_pid_logging_callback(                               \
    double y, double dy, double t, double dt,  double y_raw, int32_t c) \
LOGGING_CALLBACK_BODY(                                                  \
    "%.3f, %.1f, %.3f, %.1f, %.3f, %.3f, %.3f\n",                       \
    (double)t, 100 * (double)X, (double)y, (double)WHAT ##_pid.set,     \
    (double)(WHAT ##_pid.K_p * (WHAT ##_pid.set - y)),                  \
    (double)(WHAT ##_pid.K_p *                                          \
             WHAT ##_pid.integral / WHAT ##_pid.T_i),                   \
    (double)(-WHAT ##_pid.K_p * WHAT ##_pid.T_d * dy / dt))

DEFINE_PID_LOGGING_CALLBACK(temperature, get_heat_power())
DEFINE_PID_LOGGING_CALLBACK(pressure, get_pump_flow())
DEFINE_PID_LOGGING_CALLBACK(flow, get_pump_flow())

#undef DEFINE_SENSOR_LOGGING_CALLBACK
#undef DEFINE_PID_LOGGING_CALLBACK
#undef LOGGING_CALLBACK_BODY

static const struct pid *pid_print_target;
static bool pid_print_callback(void)
{
    uprintf(
        "%f, %f, %f, %f, %f\n",
        (double)pid_print_target->set,
        (double)pid_print_target->K_p,
        (double)pid_print_target->T_i,
        (double)pid_print_target->T_d,
        (double)pid_print_target->integral);

    return true;
}

static uint8_t i2c_print_target;
static bool i2c_print_callback(void)
{
    uprintf("%d,%x,%b\n", i2c_print_target, i2c_print_target, i2c_print_target);

    return true;
}

static uint8_t spi_print_target;
static bool spi_print_callback(void)
{
    uprintf("%d,%x,%b\n", spi_print_target, spi_print_target, spi_print_target);

    return true;
}

static uint8_t setting_print_target;
static bool setting_print_callback(void)
{
    uprintf("%d\n", setting_print_target);

    return true;
}

static bool profile_print_callback(void)
{
    print_profile();

    return true;
}

static bool profile_log_print_callback(void)
{
    print_profile_log();

    return true;
}

static bool profile_stored_callback(void)
{
    const struct profile *profile = get_profile();
    uprintf("%u\n", profile->alloc);

    return true;
}

static void usb_data_in(uint8_t *data, size_t n)
{
    uassert(n > 0);

    const char *c = (char *)data;

    /* Commands:
       b: reboot into programming mode.
       l[t][N]: toggle logging of [N] lines of [temperature] data.
       hN:  set heater command to N (0-100).
       rN:  do relay (bang-bang) control with set-point N (deg. Celsius). */

    switch(*(c++)) {
    case 'b':
         __asm__ volatile ("bkpt #251");
        break;

    case 'l':
        if (log_line_count == 0) {
            unsigned long i;
            char *e;

            switch (*(c++)) {
            case 't':
                add_callback(
                    temperature_logging_callback, temperature_callbacks);
                break;
            case 'p':
                add_callback(pressure_logging_callback, pressure_callbacks);
                break;
            case 'm':
                add_callback(mass_logging_callback, mass_callbacks);
                break;
            case 'f':
                add_callback(flow_logging_callback, flow_callbacks);
                break;
            case 'T':
                add_callback(
                    temperature_pid_logging_callback, temperature_callbacks);
                break;
            case 'P':
                add_callback(pressure_pid_logging_callback, pressure_callbacks);
                break;
            case 'F':
                add_callback(flow_pid_logging_callback, flow_callbacks);
                break;
            case 's':
                add_callback(shot_logging_callback, tick_callbacks);
                break;
            case 'c':
                add_callback(panel_logging_callback, panel_callbacks);
                add_callback(click_logging_callback, click_callbacks);
                add_callback(turn_logging_callback, turn_callbacks);
                break;
            default: goto skip;
            }

            i = strtoul(c, &e, 10);
            if (e == c) {
                log_line_count = -1;
            } else {
                log_line_count = i;
            }
          skip:
        } else {
            log_line_count = 0;
        }

        break;

    case 's':
#define SET_OR_GET(WHAT) {                                              \
            char *e;                                                    \
            double f = strtod(c, &e);                                   \
                                                                        \
            if (e == c) {                                               \
                setting_print_target = get_## WHAT() * 100.0;           \
                add_callback(setting_print_callback, tick_callbacks);   \
            } else {                                                    \
                set_## WHAT(f / 100.0);                                 \
            }                                                           \
                                                                        \
            break;                                                      \
        }

        switch(*(c++)) {
        case 'h':
        {
            switch(*(c++)) {
            case 'p':
                SET_OR_GET(heat_power);
                break;
            case 'd':
                SET_OR_GET(heat_delay);
                break;
            }

            break;
        }

        case 'p':
        {
            switch(*(c++)) {
            case 'f':
                SET_OR_GET(pump_flow);
                break;
            case 'p':
                SET_OR_GET(pump_power);
                break;
            case 'd':
                SET_OR_GET(pump_delay);
                break;
            }

            break;
        }
        }

#undef SET_OR_GET
        break;

    case 'c':
        struct pid *pid;

        switch(*(c++)) {

        case 'h':
            pid = &temperature_pid;
            goto set;
        case 'p':
            pid = &pressure_pid;
            goto set;
        case 'f':
            pid = &flow_pid;
            goto set;
        set:
            {
                double f;
                char *e;

                double * const p[] = {
                    &pid->set,
                    &pid->K_p,
                    &pid->T_i,
                    &pid->T_d};

                for (size_t i = 0; i < sizeof(p) / sizeof(p[0]); i++) {
                    f = strtod(c, &e);

                    if (e == c) {
                        break;
                    }

                    *p[i] = f;

                    if (*e != ',') {
                        break;
                    }

                    c = ++e;
                }

                pid->integral = 0;

                pid_print_target = pid;
                add_callback(pid_print_callback, tick_callbacks);

                break;
            }

        case 'i':
            {
                char *e;
                uint8_t a[3];
                int i;

                for (i = 0; i < 3; i++) {
                    a[i] = strtol(c, &e, 16);

                    if (e == c || (*e != ',' && *e != '\0')) {
                        break;
                    }

                    c = ++e;
                }

                if (i == 3) {
                    write_i2c(a[0], a[1], a[2]);
                } else if (i == 2) {
                    read_i2c(a[0], a[1], &i2c_print_target, 1);
                    add_callback(i2c_print_callback, tick_callbacks);
                } else if (i == 1) {
                    probe_i2c(a[0]);
                }

                break;
            }

        case 's':
            {
                char *e;
                uint8_t a[2];
                int i;

                for (i = 0; i < 2; i++) {
                    a[i] = strtol(c, &e, 16);

                    if (e == c || (*e != ',' && *e != '\0')) {
                        break;
                    }

                    c = ++e;
                }

                /* Select the MAX31865; the display can't be operated
                 * via simple SPI reads/writes. */

                const uint32_t b = SPI_PUSHR_PCS(0) | SPI_PUSHR_CTAS(1);

                if (i == 2) {
                    /* Write register a[0] with value a[1]. */

                    SPI0_SR |= SPI_SR_TFFF;
                    WAIT_WHILE(!(SPI0_SR & SPI_SR_TFFF), 100);
                    SPI0_PUSHR = b | SPI_PUSHR_CONT | a[0];

                    SPI0_SR |= SPI_SR_TFFF;
                    WAIT_WHILE(!(SPI0_SR & SPI_SR_TFFF), 100);
                    SPI0_PUSHR = b | a[1];
                } else if (i == 1) {
                    /* Read register a[0]. */

                    delay_us(500);

                    SPI0_SR |= (SPI_SR_TFFF | SPI_SR_EOQF);
                    WAIT_WHILE(!(SPI0_SR & SPI_SR_TFFF), 100);
                    SPI0_PUSHR = (b | SPI_PUSHR_CONT | SPI_PUSHR_EOQ | a[0]);

                    WAIT_WHILE(!(SPI0_SR & SPI_SR_EOQF), 100);
                    SPI0_MCR |= SPI_MCR_CLR_RXF;
                    SPI0_SR |= SPI_SR_EOQF;

                    SPI0_SR |= SPI_SR_TFFF;
                    WAIT_WHILE(!(SPI0_SR & SPI_SR_TFFF), 100);
                    SPI0_PUSHR = b;

                    SPI0_SR |= SPI_SR_RFDF;
                    WAIT_WHILE(!(SPI0_SR & SPI_SR_RFDF), 100);

                    spi_print_target = SPI0_POPR;
                    add_callback(spi_print_callback, tick_callbacks);
                }

              error:

                break;
            }
        }

        break;

    case 'z':
        switch(*(c++)) {

        case 'f':
            tare_flow();
            break;

        case 'm':
            tare_mass();
            break;
        }

        break;

    case 't':
        switch(*(c++)) {

        case 's':
            /* Toggle sensor power. */

            GPIOC_PTOR = PT(2);
            break;

        case 'd':
            /* Toggle display update. */

            update_display = !update_display;
            break;

        case 't':
        {
            unsigned long i;
            char *e;

            i = strtoul(c, &e, 10);
            if (e > c) {
                run_temperature((bool)i);
            } else {
                read_temperature();
            }

            break;
        }

        case 'p':
        {
            unsigned long i;
            char *e;

            i = strtoul(c, &e, 10);
            if (e > c) {
                run_pressure((bool)i);
            } else {
                read_pressure();
            }

            break;
        }

        case 'm':
        {
            unsigned long i;
            char *e;

            i = strtoul(c, &e, 10);
            if (e > c) {
                run_mass((bool)i);
            } else {
                read_mass();
            }

            break;
        }
        }

        break;

    case 'p':
        switch (*c) {
        case ',':
            if (read_profile(c)) {
                add_callback(profile_stored_callback, tick_callbacks);
            }

            break;
        case 'l':
            add_callback(profile_log_print_callback, tick_callbacks);
            break;
        default:
            add_callback(profile_print_callback, tick_callbacks);
            break;
        }

        break;

    case 'r':
        /* Request a system reset. */

        SCB_AIRCR = 0x5fa0004;
        break;
    }
}

static enum {
    AUTO,
    MANUAL_TEMPERATURE,
    MANUAL_FLOW,
    MANUAL_PRESSURE,
    MANUAL_HEAT,
    MANUAL_PUMP,

    MODES
} mode;

static bool temperature_pid_callback(
    double T, double dT, double t, double dt, double T_raw, uint16_t c)
{
    if (isnan(temperature_pid.set) || isnan(dt)) {
        return false;
    }

    uassert(dt > 0);

    set_heat_power(
        isnan(T) || isnan(dT)
        ? 0
        : calculate_pid_output(&temperature_pid, T, dT, dt));

    return false;
}

static bool pressure_pid_callback(
    double P, double dP, double t, double dt, double P_raw, uint16_t c)
{
    if (isnan(pressure_pid.set) || isnan(dt)) {
        return false;
    }

    uassert(dt > 0);

    set_pump_flow(
        isnan(P) || isnan(dP)
        ? 0
        : fmax(0.01, calculate_pid_output(&pressure_pid, P, dP, dt)));

    return false;
}

static bool flow_pid_callback(
    double Q, double dQ, double t, double dt,  double V, double raw, uint32_t n)
{
    if (isnan(flow_pid.set) || isnan(dt)) {
        return false;
    }

    uassert(dt > 0);

    set_pump_flow(
        isnan(Q) || isnan(dQ)
        ? 0
        : fmax(0.01, calculate_pid_output(&flow_pid, Q, dQ, dt)));

    return false;
}

static bool mode_switch_callback(bool down)
{
    if (down) {
        return false;
    }

    do {
        mode = (mode + 1) % MODES;
    } while (!isnan(get_shot_time())
             && mode != AUTO
             && mode != MANUAL_FLOW
             && mode != MANUAL_PRESSURE
             && mode != MANUAL_PUMP);

    enable_profile(mode == AUTO);

    return false;
}
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
int main(void)
{
    /* Configure interrupt priority grouping.  We select one group
     * bit, meaning that priorities >= 8 belong to the low-priority
     * group and can be preempted by IRQs with priority < 8. */

    SCB_AIRCR = 0x5fa0600;
    enable_interrupts();

    /* SysTick timer */

#ifdef TEENSY30
    SYST_RVR = 4800000 - 1;
#else
    SYST_RVR = 7200000 - 1;
#endif
    SYST_CVR = 0;
    SYST_CSR = SYST_CSR_CLKSOURCE | SYST_CSR_TICKINT | SYST_CSR_ENABLE;

    /* PIT */

    SIM_SCGC6 |= SIM_SCGC6_PIT;
    PIT_MCR &= ~PIT_MCR_MDIS;

    /* SPI */

    SIM_SCGC5 |= SIM_SCGC5_PORTD | SIM_SCGC5_PORTC;
    SIM_SCGC6 |= SIM_SCGC6_SPI0;

    PORTC_PCR6 = PORT_PCR_MUX(2) | PORT_PCR_DSE; /* DOUT */
    PORTC_PCR7 = PORT_PCR_MUX(2) | PORT_PCR_DSE; /* DIN */
    PORTD_PCR1 = PORT_PCR_MUX(2) | PORT_PCR_DSE; /* SCK */

    SPI0_MCR &= ~SPI_MCR_MDIS;
    SPI0_MCR = SPI_MCR_MSTR;

    reset_time();
    reset_usb();
    set_usb_data_in_callback(usb_data_in);

#if 0
    await_usb_dtr();
#endif

    /* Initialize the peripherals. */

    reset_input();
    reset_power();
    reset_temperature();
    reset_i2c();
    reset_flow();
    reset_display();
    reset_profile();
    enable_profile(mode == AUTO);

    add_callback(temperature_pid_callback, temperature_callbacks);
    add_callback(pressure_pid_callback, pressure_callbacks);
    add_callback(flow_pid_callback, flow_callbacks);
    add_callback(mode_switch_callback, click_callbacks);
    add_callback(adjust_callback, turn_callbacks);

    clear_display();

    display("\a\4\x0a\1Time:\a\x44\x0a\1Temp:");
    display("\a\4\x2a\1Flow:\a\x44\x2a\1Pres:");
    display("\a\4\x4a\1Vol:\a\x44\x4a\1Mass:");
    display("\a\4\x6a\1Heat:\a\x44\x6a\1Pump:");

    display("\x3f\a\4\x1d\2-  \v");

    while (true) {
        if (!update_display) {
            delay_ms(100);
            continue;
        }

        static bool p_0;
        const bool p = fmod(get_time(), 0.5) < 0.25;

#define UPDATE_DISPLAY(X, BLINK, POS, VALUE, UNIT)                      \
        static double X ##_0 = -INFINITY;                               \
        const double X = VALUE;                                         \
                                                                        \
        if (((BLINK) && p != p_0)                                       \
            || (!(isnan(X ##_0) && isnan(X)) && X ##_0 != X)) {         \
            if (BLINK && p) {                                           \
                display("\a" POS "\2\v");                               \
                X ##_0 = -INFINITY;                                     \
            } else {                                                    \
                if (isnan(X)) {                                         \
                    display("\a" POS "\2-  \v");                        \
                } else {                                                \
                    if (fabs(X) < 1000) {                               \
                        display("\a" POS "\2%.1f\1" UNIT "\v", (double)X); \
                    } else {                                            \
                        display("\a" POS "\2%.0f\1" UNIT "\v", (double)X); \
                    }                                                   \
                }                                                       \
                                                                        \
                X ##_0 = X;                                             \
            }                                                           \
        }

        /* Shot time */

        UPDATE_DISPLAY(t, false, "\4\x1d", get_shot_time(), "s");

        /* Temperature */

        UPDATE_DISPLAY(
            T, mode == MANUAL_TEMPERATURE, "\x44\x1d",
            (mode == MANUAL_TEMPERATURE
             ? temperature_pid.set
             : (temperature_filter.y < 0 ? 0 : temperature_filter.y)),
            "\2\x7f");

        /* Flow */

        {
            const double x = (mode == MANUAL_FLOW ? flow_pid.set : get_flow());

            UPDATE_DISPLAY(
                Q, mode == MANUAL_FLOW, "\4\x3d",
                (x >= 10 ? 9.9 : x),
                "ml/s");
        }

        /* Pressure */

        UPDATE_DISPLAY(
            S, mode == MANUAL_PRESSURE, "\x44\x3d",
            (mode == MANUAL_PRESSURE
             ? pressure_pid.set
             : (pressure_filter.y < 0 ? 0 : pressure_filter.y)),
            "bar");

        /* Mass */

        UPDATE_DISPLAY(
            M, is_taring_mass(), "\x44\x5d", mass_filter.y, "g");

        /* Volume */

        UPDATE_DISPLAY(V, false, "\4\x5d", get_volume(), "ml");

        /* Heating power */

        UPDATE_DISPLAY(
            H, mode == MANUAL_HEAT, "\4\x7d",
            get_heat_power() * 100, "%%");

        /* Pump power */

        UPDATE_DISPLAY(
            W, mode == MANUAL_PUMP,"\x44\x7d",
            get_pump_flow() * 100, "%%");

        p_0 = p;

#undef UPDATE_DISPLAY
    }
}

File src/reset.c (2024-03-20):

/* Copyright (C) 2024 Papavasileiou Dimitris
 *
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
 * You should have received a copy of the GNU General Public License
 * along with this program.  If not, see <http://www.gnu.org/licenses/>.
 */

#include "mk20dx.h"
#include "uassert.h"

extern void __libc_init_array (void);
extern void __libc_fini_array (void);
extern char __bss_start, __bss_end;
extern char __data_start, __data_end, __data_load;
extern int main (void);
extern unsigned long __stack_end;

static __attribute__ ((section(".flashconfig"), used))
const uint8_t flashconfigbytes[16] = {
    /* Backdoor comparison key */

    0xff, 0xff, 0xff, 0xff, 0xff, 0xff, 0xff, 0xff,

    /* Program flash protection bytes */

    0xff, 0xff, 0xff, 0xff,

    /* FSEC */

    0x42,

    /* FOPT */

    0xf9,

    /* EEPROM protection byte */

    0xff,

    /* Data flash protection byte */

    0xff
};

static __attribute__((interrupt ("IRQ"))) void unused_isr(void)
{
    uassert(0);
}

static __attribute__((noreturn, interrupt ("IRQ"))) void fault_isr(void)
{
    uassert(0);
}

void pdb0_isr(void) __attribute__ ((weak, alias("unused_isr")));
void i2c0_isr(void) __attribute__ ((weak, alias("unused_isr")));
void ftm0_isr(void) __attribute__ ((weak, alias("unused_isr")));
void ftm1_isr(void) __attribute__ ((weak, alias("unused_isr")));
void pit0_isr(void) __attribute__ ((weak, alias("unused_isr")));
void pit1_isr(void) __attribute__ ((weak, alias("unused_isr")));
void pit2_isr(void) __attribute__ ((weak, alias("unused_isr")));
void pit3_isr(void) __attribute__ ((weak, alias("unused_isr")));
void porta_isr(void) __attribute__ ((weak, alias("unused_isr")));
void portb_isr(void) __attribute__ ((weak, alias("unused_isr")));
void portc_isr(void) __attribute__ ((weak, alias("unused_isr")));
void portd_isr(void) __attribute__ ((weak, alias("unused_isr")));
void usb_isr(void) __attribute__ ((weak, alias("unused_isr")));
void systick_isr(void) __attribute__ ((weak, alias("unused_isr")));

void reset(void)
{
    /* Unlock the watchdog and disable it.  After unlocking, we need
     * to wait 1 bus clock cycle before updating the status register
     * (see manual pg. 466).  After reset bus and core clocks are
     * equal, so this translates to 1 system clock cycle. */

    WDOG_UNLOCK = (uint16_t)0xc520;
    WDOG_UNLOCK = (uint16_t)0xd928;
    __asm__ volatile ("nop");
    WDOG_STCTRLH = WDOG_STCTRLH_ALLOWUPDATE;

    /* Reset on low voldage detection. */

    PMC_LVDSC1 |= PMC_LVDSC1_LVDRE;

    /* Configure the clock, see manual pg. 510. */

    OSC0_CR = OSC_SC8P | OSC_SC2P | OSC_ERCLKEN; /* Enable the crystal. */

#ifdef TEENSY30
    /* Select clock dividers for 48Mhz core, 48Mhz bus, 24 Mhz flash
     * clocks. */

    SIM_CLKDIV1 = SIM_CLKDIV1_OUTDIV1(0) | SIM_CLKDIV1_OUTDIV2(0) |
                  SIM_CLKDIV1_OUTDIV4(1);
#else
    /* Select clock dividers for 72Mhz core, 48Mhz bus, 24 Mhz flash
     * clocks.  See manual pg. 157-158 for maximum allowed
     * frequencsies. */

    SIM_CLKDIV1 = SIM_CLKDIV1_OUTDIV1(1) | SIM_CLKDIV1_OUTDIV2(2) |
                  SIM_CLKDIV1_OUTDIV4(5);
#endif

    /* Select the crystal as external references, very high frequency
     * range. */

    MCG_C2 = MCG_C2_RANGE0(2) | MCG_C2_EREFS0;

    /* Switch to external reference as clock source, FLL input = 16 MHz / 512 */

    MCG_C1 = MCG_C1_CLKS(2) | MCG_C1_FRDIV(4);

    /* Wait for crystal oscillator to initialize and sources to be
     * selected. */

    while (!(MCG_S & MCG_S_OSCINIT0));
    while (MCG_S & MCG_S_IREFST);
    while ((MCG_S & MCG_S_CLKST_MASK) != MCG_S_CLKST(2));

    /* Now in FBE mode, clocked by the crystal at 16Mhz with the FLL
     * bypassed. */

#ifdef TEENSY30
    /* Configure the PLL divider for 16 MHz / 8 = 2 MHz and the output
     * multiplier for 48 Mhz. */

    MCG_C5 = MCG_C5_PRDIV0(7);
    MCG_C6 = MCG_C6_PLLS | MCG_C6_VDIV0(0);
#else
    /* Configure the PLL divider for 16 MHz / 5 = 3.2 MHz and the
     * output multiplier for 144 Mhz. */

    MCG_C5 = MCG_C5_PRDIV0(4);
    MCG_C6 = MCG_C6_PLLS | MCG_C6_VDIV0(21);
#endif

    /* Wait for PLL lock and source selection and we're in PBE
     * mode. */

    while (!(MCG_S & MCG_S_PLLST));
    while (!(MCG_S & MCG_S_LOCK0));

    /* Switch to PLL as clock source, wait for PLL clock to be
     * selected and we're in PEE mode. */

    MCG_C1 = MCG_C1_CLKS(0) | MCG_C1_FRDIV(4);
    while ((MCG_S & MCG_S_CLKST_MASK) != MCG_S_CLKST(3));

    /* Copy the data section to RAM and clear the bss section. */

    for (char *c = &__bss_start; c < &__bss_end; *c++ = 0);
    for (char *c = &__data_start, *d = &__data_load;
         c < &__data_end;
         *c++ = *d++);

    /* Configure the LED pin as an output. */

    SIM_SCGC5 |= SIM_SCGC5_PORTC;
    PORTC_PCR5 = PORT_PCR_MUX(1);
    GPIOC_PDDR |= PT(5);

    __libc_init_array();

    main();

    __libc_fini_array();

    while(1);
}

__attribute__ ((section(".vectors"), used))
void (* const vectors[])(void) =
{
    (void (*)(void))&__stack_end, /* ARM core Initial Stack Pointer */
    reset,   /* ARM core Initial Program Counter */
    unused_isr, /* ARM core Non-maskable Interrupt (NMI) */
    fault_isr, /* ARM core Hard Fault */
    fault_isr, /* ARM core MemManage Fault */
    fault_isr, /* ARM core Bus Fault */
    fault_isr, /* ARM core Usage Fault */
    unused_isr, /* - - */
    unused_isr, /* - - */
    unused_isr, /* - - */
    unused_isr, /* - - */
    unused_isr, /* ARM core Supervisor call (SVCall) */
    unused_isr, /* ARM core Debug Monitor */
    unused_isr, /* - - */
    unused_isr, /* ARM core Pendable request for system service */
    systick_isr, /* ARM core System tick timer (SysTick) */
    unused_isr, /* DMA DMA channel 0 transfer complete */
    unused_isr, /* DMA DMA channel 1 transfer complete */
    unused_isr, /* DMA DMA channel 2 transfer complete */
    unused_isr, /* DMA DMA channel 3 transfer complete */

#ifndef TEENSY30
    unused_isr, /* DMA DMA channel 4 transfer complete */
    unused_isr, /* DMA DMA channel 5 transfer complete */
    unused_isr, /* DMA DMA channel 6 transfer complete */
    unused_isr, /* DMA DMA channel 7 transfer complete */
    unused_isr, /* DMA DMA channel 8 transfer complete */
    unused_isr, /* DMA DMA channel 9 transfer complete */
    unused_isr, /* DMA DMA channel 10 transfer complete */
    unused_isr, /* DMA DMA channel 11 transfer complete */
    unused_isr, /* DMA DMA channel 12 transfer complete */
    unused_isr, /* DMA DMA channel 13 transfer complete */
    unused_isr, /* DMA DMA channel 14 transfer complete */
    unused_isr, /* DMA DMA channel 15 transfer complete */
#endif

    unused_isr, /* DMA DMA error interrupt channels 0-15 */
    unused_isr, /* - - */
    unused_isr, /* Flash memory Command complete */
    unused_isr, /* Flash memory Read collision */
    unused_isr, /* Mode Controller Low-voltage detect, low-voltage warning */
    unused_isr, /* LLWU Low Leakage Wakeup */
    unused_isr, /* WDOG or EWM */
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

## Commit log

2024-03-20 Import the sources into Git.
    [board.kicad_pcb, board.kicad_sch, snubber.sch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]
2024-03-20 Add prebuilt STL files.
    [controller_bracket.stl, knob.stl, knob_sleeve.stl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]
2024-11-17 Improve the enclosure; switch to heat-set threaded inserts.
2024-11-20 Enable encoder input pull-ups.

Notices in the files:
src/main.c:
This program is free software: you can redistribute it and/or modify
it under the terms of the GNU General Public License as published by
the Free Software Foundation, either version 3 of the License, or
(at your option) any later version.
